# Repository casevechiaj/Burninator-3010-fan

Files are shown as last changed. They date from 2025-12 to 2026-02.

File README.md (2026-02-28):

# Burninator v2.2 💪🐉🔥
This toolhead is yet another 4010 toolhead, heavily inspired by the [Dragonburner](https://github.com/chirpy2605/voron/tree/main/V0/Dragon_Burner) and the [A4T](https://github.com/Armchair-Heavy-Industries/A4T/tree/main), all props to them.  
Thanks to Reddit user pd1zzle for suggesting the toolhead name, I really took a liking to it.  
And thanks to Reddit user linuxgangster for suggesting, testing, and providing feedback for the MadMax toolchanger adaptation.
 
<p>
 

</p>
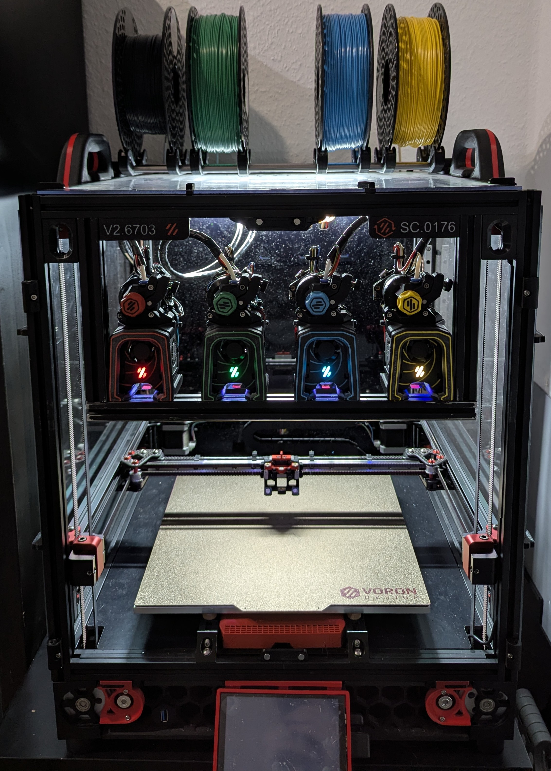
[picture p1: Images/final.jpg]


## But why?  
I created this toolhead because I wasn’t quite happy with the current toolhead options for my Stealthchanger.
Therefore, I decided to create my own toolhead to suit my use case and my printer.
I took features from the Dragonburner and the A4T and put them together, resulting in the Burninator.

## What its features?
It is small, smaller than the already compact Dragonburner, yet it can hold a UHF hotend, in this case the Dropeffect Next G Fiber with the UHF adapter, without missing out on nozzle and logo LEDs.
A monolithic cowl like the A4T cuts down the number of printed parts, screws, and heat inserts, increases rigidity, and simplifies assembly and disassembly.
Having a wall thickness of 1.2 mm makes the cowl more robust.  
It also adopts the A4Ts backflow inhibitor for decent part cooling performance.  



## Hotend compatibility:
- For the SF cowl, any Pheatus Dragon like hotends should fit i.e.: NextG, TZ.
- For the UHF cowl, any Pheatus Dragon UHF like hotend should fit i.e.: NextG UHF, Rapido HF, Dragon ACE (with the spacer)
- The CHC-XL got it own cowls 
- Rapido UHF got it own cowls

## Anything else?  
Besides the Rapido UHF, CHC-XL, UHF and SF toolheads, there are: 
- MGN12H invertable (Voron-2 / Monolith Gantry mod), MGN9H (pandora's gantry mod) and MGN7H (Voron-0) carriage, with x-endstop and both, klicky or Beacon/Cartographer(+spacer) mount, for standalone, non-toolchanger printers 
- StealthChanger toolchanger: backplate, ajustable docks with inbuild PTFE whiper and spring steel blocker, adapter for DraftShft docks
- MadMax toolchanger: backplate, docks with inbuild spring steel blocker and optinal PTFE whiper, modified SF and UHF cowls to work with MadMax.

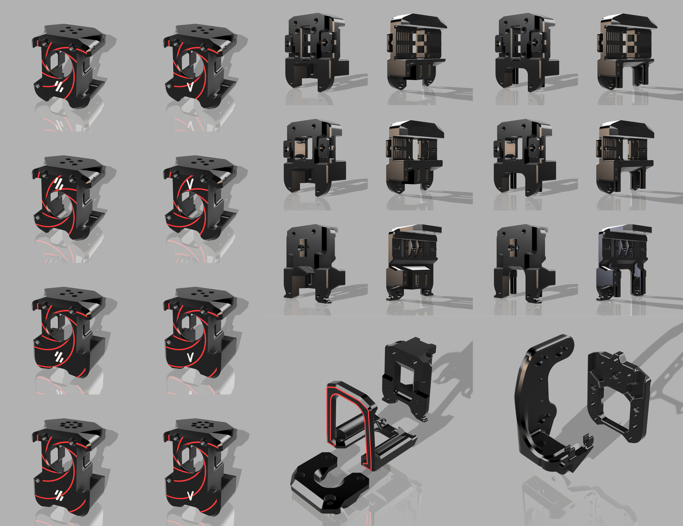
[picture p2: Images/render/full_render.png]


## What is planed?
For now, not much. 
You can also do request and I can take a look at it and upload it in the future. 
Of course, CAD files are available for you to mod it to your needs.

## How to Assemble?
Here's the [BOM](https://github.com/The-Duke-96/Burninator/blob/main/BOM.md).      
Here's a handy-dandy [Assembly manual](https://github.com/The-Duke-96/Burninator/blob/main/Assembly%20Manual.md).   

## Disclaimer:
- It turns out that when using printed parts for the Z-joints, the toolhead might be so small that the carriage of the Z linear rail hits the bottom of the frame before the toolhead touches the print bed for probing or leveling, since I have used a CNC kit for those parts from the beginning, I didn’t notice or consider it, a simple workaround is to add taller spacers or washers beneath the print bed, or use a diffrent, shorter Z-joints.
- Because the dock is quite small and space-saving, when using a door buffer for the StealthChanger, the DraftShift_dock_adapter needs to be used, otherwise the shuttle won’t reach the toolheads.
- If you use Beacon/Cartographer on CHC-XL or Rapido-UHF cowl, you need to extend the spacers to the correct lenght.
- StealthChanger and MadMax docks are designed for the SF and UHF cowls. I do not plan to adapt them for CHC XL or Rapido UHF, simply because a toolchanger already sacrifices print volume, and the smaller SF and UHF cowls are better suited for that use case. 
- For many files I have not received any feedback and, or could not test them myself, so if something is not working or not fitting, please let me know.
- Stock StealthChanger pickup and dropoff paths should work just fine, it might need some adjusment for the nozzle to scrub over the whiper.  If you like, you can use my custom paths:

```
params_dropoff_path: [{'y': 25, 'z':3}, {'y': 5, 'z':3} , {'y':0, 'z':3, 'f':0.5}, {'y':0, 'z':0, 'f':0.5}, {'y':0, 'z':-10}]
params_pickup_path: [{'y':0, 'z':-10}, {'y':0, 'z':0, 'f':0.5, 'verify':1}, {'y':0, 'z':3, 'f':0.5}, {'y': 25, 'z':3}]
```

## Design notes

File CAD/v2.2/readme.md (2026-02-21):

# CAD .step file

- Use these files if you wish to modify something. 
- “Burninator_RAW.step” offers a clean base version of the Burninator, with no cosmetics, no spiral pattern, no extruder mounts, and no front LED logo, so you can use it as a foundation to build on.
- Keep in mind that the fan duct must blow air to the correct area: the tip of the hotend nozzle should sit about 1.5 mm beneath the lowest part of the cowl.
- The CAD files do not include the subtraction for the MadMax screw holes on the cowls, in order to keep the file size down.
The component called “cowl_screwhole_extensions” in Burninator, MadMax is exactly what it says. Combine it with any cowl of your choice, do the screw hole subtraction, and you are done.

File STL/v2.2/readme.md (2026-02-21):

# STL Files

- All printed parts are already oriented correctly for printing.
- Required print supports are built in.
- cowls and its cosmetics are uploaded in one file as .3MF, no aligning in slicer needed anymore
- For the LED diffuser, it's recommended to print it in white or clear filament. You can also leave out the logo LED and print it in any color you want.
- You do not have to print the cowls in two colors, you can combine the two objects in the slicer, or simply print both in the same color.
- If you are using Cartographer or Beacon with the Rapido UHF or CHC XL cowl, do not forget to scale the spacer to the correct length.

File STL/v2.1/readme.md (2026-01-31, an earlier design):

# STL Files

- All printed parts are already oriented correctly for printing.
- Required print supports are built in.
- Cosmetics and their corresponding parts must be printed together, just align them and decide if and how you want to color them.  
**Note:** Aligning the cosmetic to the cowl, either eyeball it or use the following reference offsets:  
UHF cowl on X0/Y0, cosmetic X-1,75/Y0.35  
SF cowl on X0/Y0, cosmetic X0/Y-2.03

- For the LED diffuser, it's recommended to print it in white or clear filament. You can also leave out the logo LED and print it in any color you want.

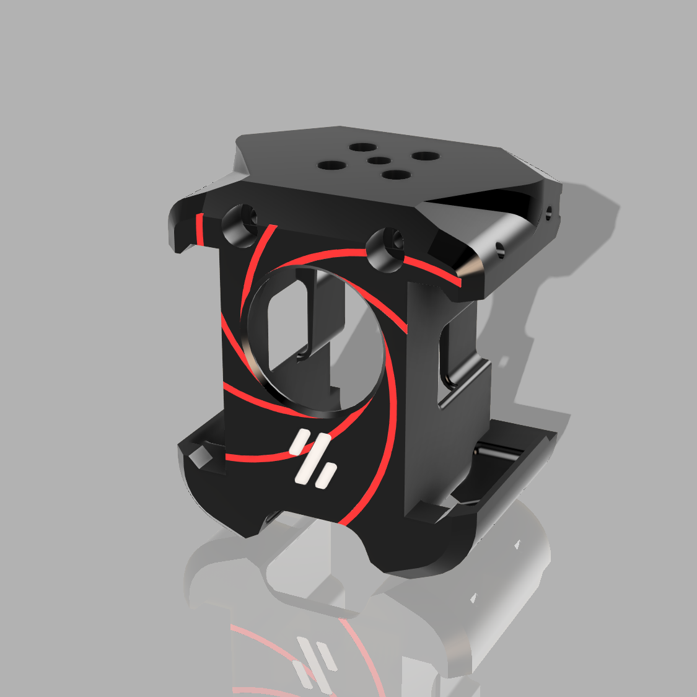
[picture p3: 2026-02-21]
Images/render/UHF_voron.png

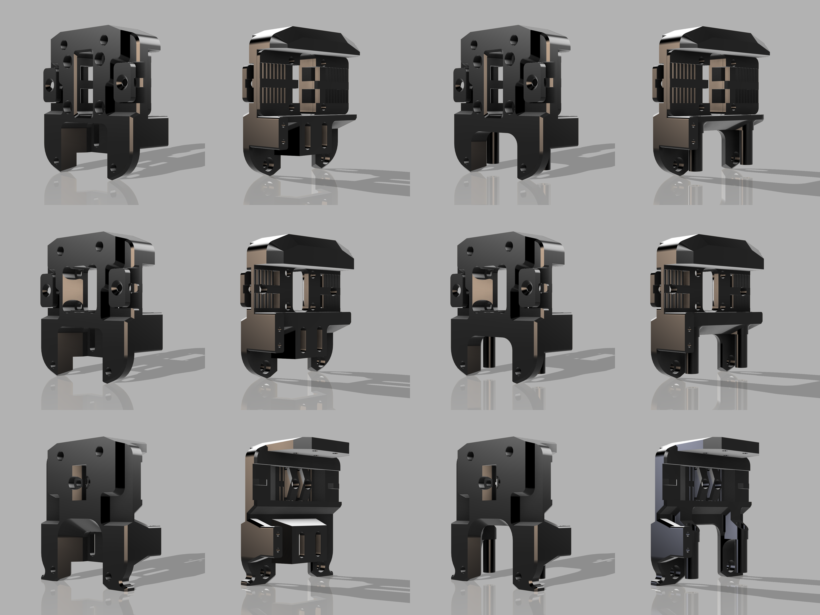
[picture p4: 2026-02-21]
Images/render/MGNxH_carriage.png

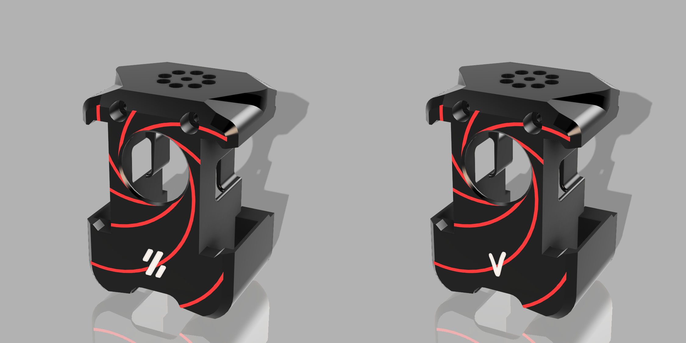
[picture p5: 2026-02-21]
Images/render/CHC-XL_cowl.png

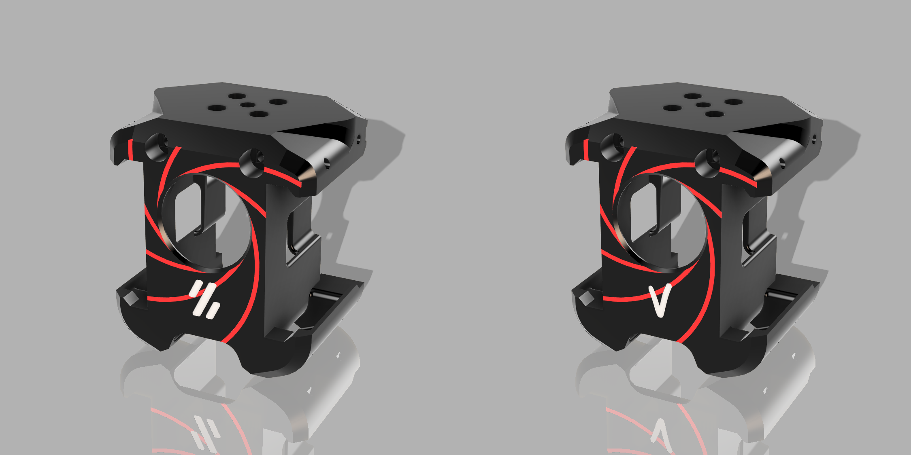
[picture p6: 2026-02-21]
Images/render/UHF_cowl.png

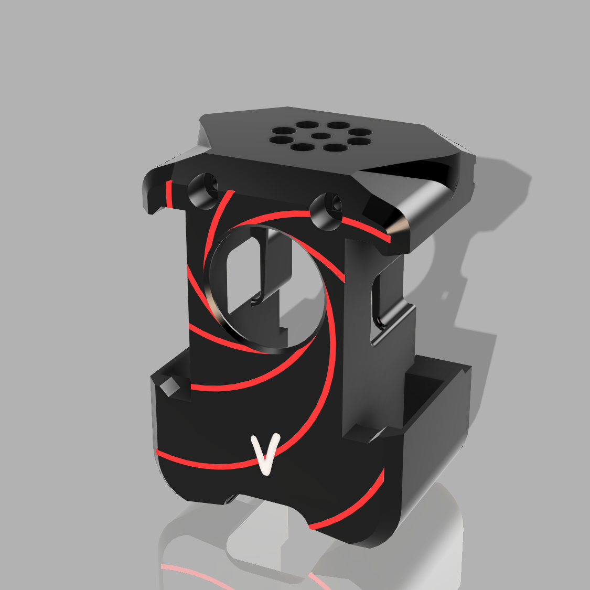
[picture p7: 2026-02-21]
Images/render/CHC-XL_consummate-V.png

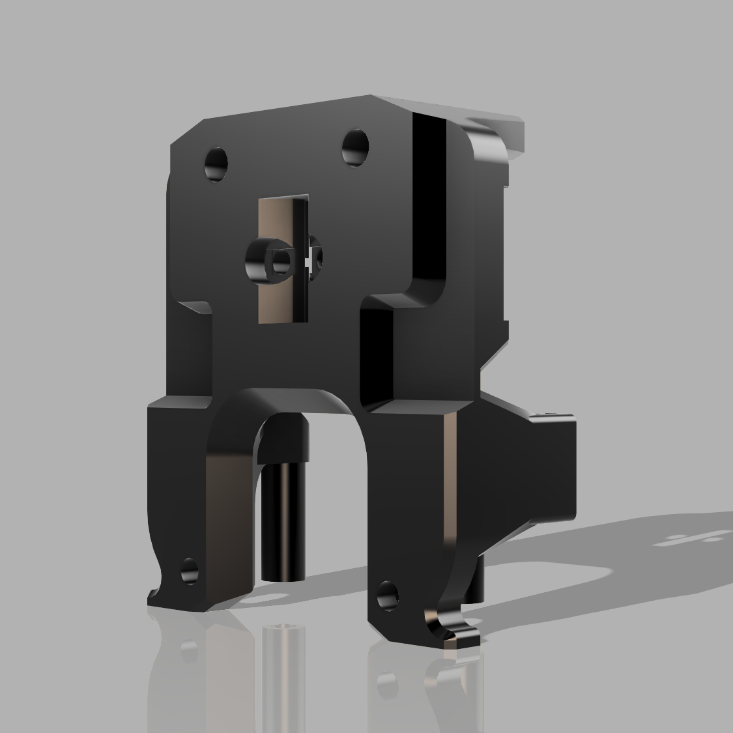
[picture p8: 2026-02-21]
Images/render/MGN7H_front_beacon_cartographer.png

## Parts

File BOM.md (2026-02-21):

# BOM

## Heat inserts
- 4x M3x4 on cowl
- 3x M3x4 on dock (stealthchanger)
- 1x M3x4 on dock (madmax)
- 2x M3x4 on stealthchanger backplate
- 2x M3x4 on MGN7H/MGN9H/MGN12H klicky carriage
- 4x M3x4 on MGN7H/MGN9H/MGN12H beacon/cartographer carriage
- 2x m3x4 on LGX Adapter
- 2x m3x4 on EBB36 mount
- 2x M5 on DraftShift Adapter

## Screws
- 2x M3x35 SHCS to secure cowl to backplate and MGN7H, MGN9H or MGN12H
- 2x M3x6 SHCS to secure cowl to backplate and MGN7H, MGN9H or MGN12H
- 2x M3x5 FHCS to secure belt clamps on MGN7H, MGN9H or MGN12H carriage
- 4x M3x10 to secure MGN9H or MGN12H carriage to linear rail
- 4x M3x6 to secure MGN7H carriage to linear rail
- 2x M3x6 SHCS to secure dock back
- 1x M3x5 BHCS to secure spring steel blocker
- 4x M5x8 BHCS to secure stealthchanger dock to DraftShift adapter and 2020 extrusion or crossbar
- 2x M5x8 BHCS to secure maxmax dock to 2020 extrusion or crossbar
- 2x M3x16 standoff on extruder back
- 2x M3x6 BHCS to secure EBB36 mount to standoffs
- 2x M3x6 BHCS to secure EBB36 PCB to mount
- 2x M3x6 BHCS to secure optotap to backplate
- 2x M3x6 SHCS to secure LGX adapter to cowl
- 2 M3x20 BHCS to secure beacon/cartographer to carriage (longer screws needed for CHC-Xl and Rapido UHF cowl)

## Others
- 1x 2510 fan 24V
- 2x 4010 fan 24V
- 3x RGB PCB LEDs (NeoPixel or simular)
- 1x PTFE tube 21mm (stealthchanger dock)
- 1x PTFE tube 25mm (madmax dock)
- 1x spring steel blocker 7x29mm cut from old tape measure (stealthchanger dock)
- 1x spring steel blocker 5x36mm cut from old tape measure (madmax dock)
- 2x magnets 3x6mm N52 (stealthchanger dock)
- 3x magnets 3x6mm N52 (madmax dock)

## Also you might want to check out those other BOMs:  
MadMax: https://github.com/zruncho3d/madmax/blob/main/BOM.md  
StealthChanger: https://github.com/DraftShift/StealthChanger/wiki/Bill-of-Materials

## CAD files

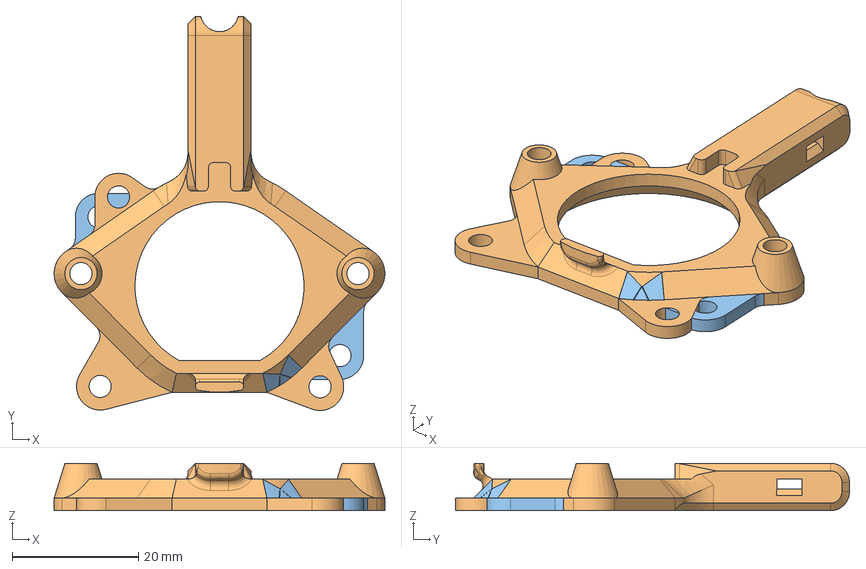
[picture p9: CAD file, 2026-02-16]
CAD/v2.2/EBB36_Mount.step
52.3 x 62.3 x 7.50 mm

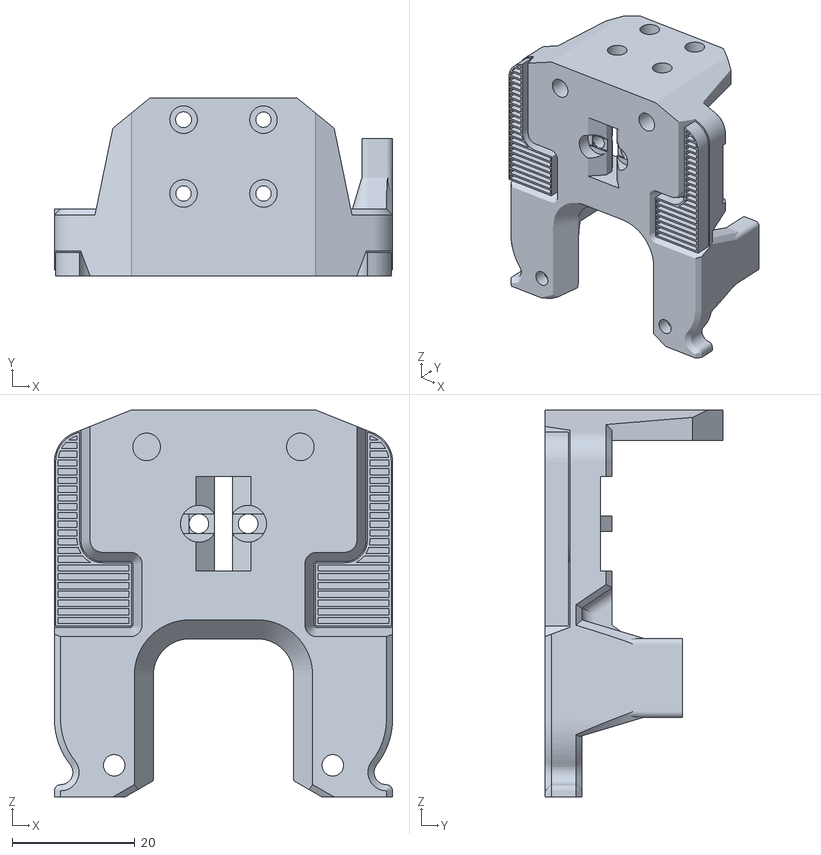
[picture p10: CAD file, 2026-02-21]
STL/v2.2/Carriage/MGN7H_carriage_beacon_cartographer.stl
55.0 x 28.9 x 62.9

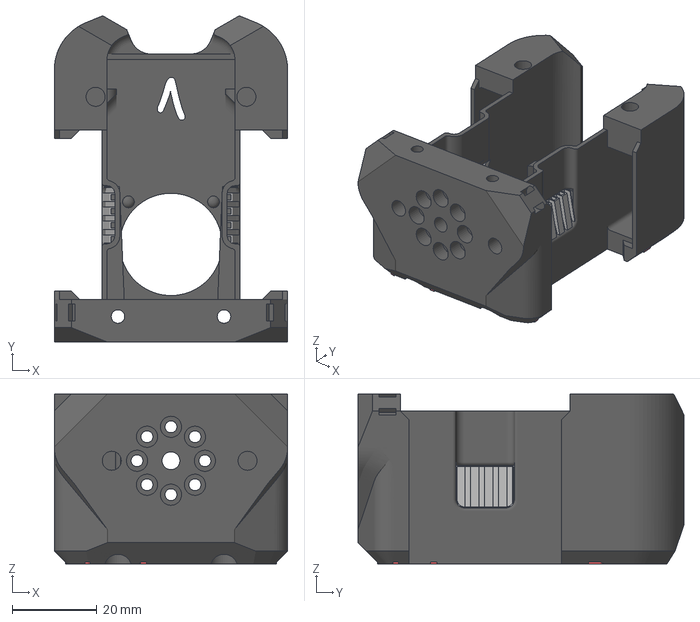
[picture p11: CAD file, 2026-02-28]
STL/v2.2/cowls_3MF/CHC-XL/consummate-V_logo/CHC_consummate-V_sherpa-micro.3mf
55.0 x 76.8 x 40.0 mm

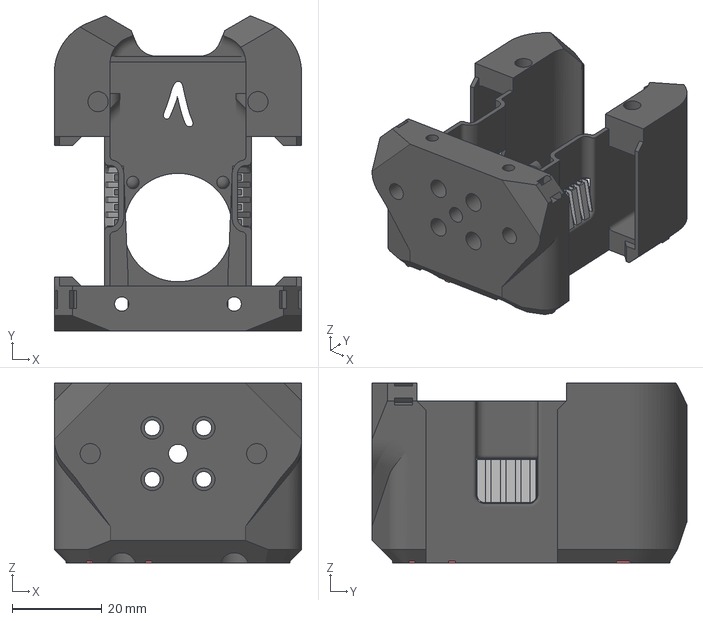
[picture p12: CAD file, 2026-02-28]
STL/v2.2/cowls_3MF/Rapido_UHF/consummate-V_logo/Rapido_UHF_consummate-V_orbiter.3mf
55.0 x 70.0 x 40.0 mm

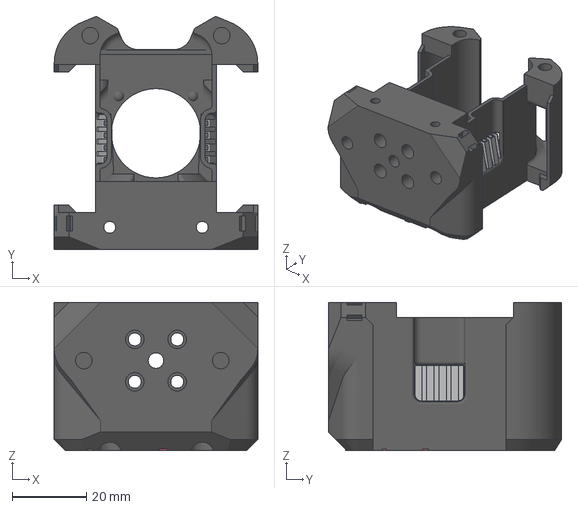
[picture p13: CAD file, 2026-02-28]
STL/v2.2/cowls_3MF/SF/consummate-V_logo/SF_consummate-V_orbiter.3mf
55.0 x 62.9 x 40.0 mm

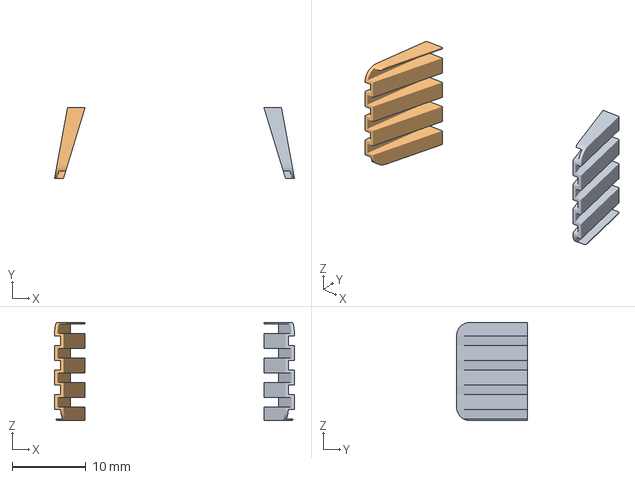
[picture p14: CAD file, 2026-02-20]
STL/v2.2/cowls_3MF/support.3mf
32.5 x 9.60 x 13.3 mm
Körper1
Körper4

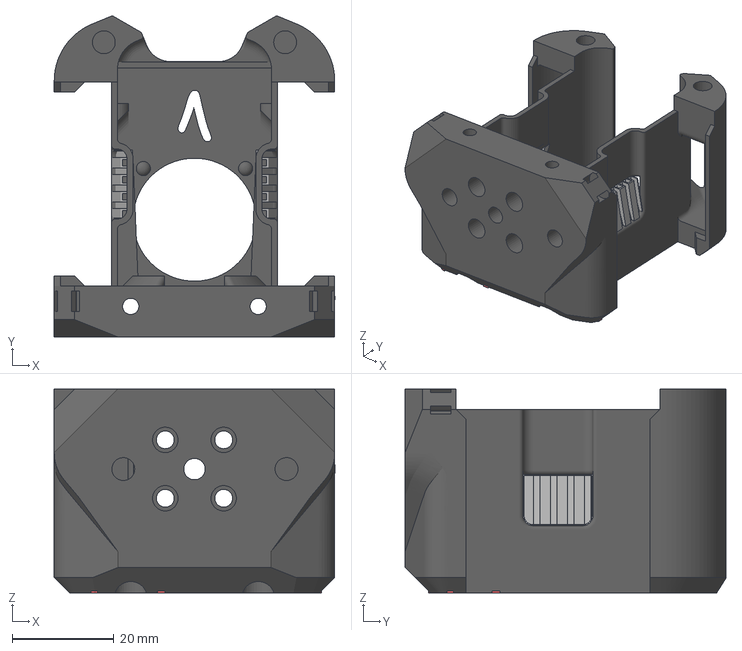
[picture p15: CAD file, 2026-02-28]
STL/v2.2/cowls_3MF/UHF/consummate-V_logo/UHF_consummate-V_sherpa_micro.3mf
55.0 x 62.9 x 40.0 mm

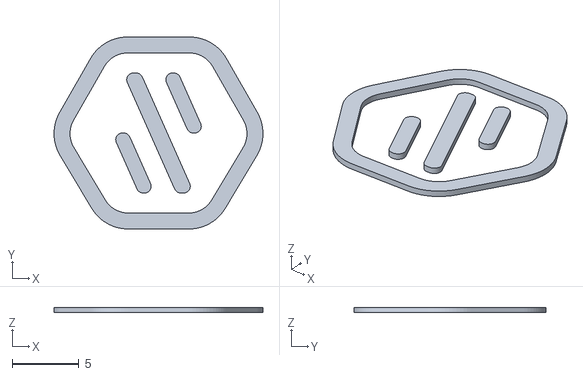
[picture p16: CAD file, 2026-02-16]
STL/v2.2/Knob_logo.stl
15.7 x 14.4 x 0.4

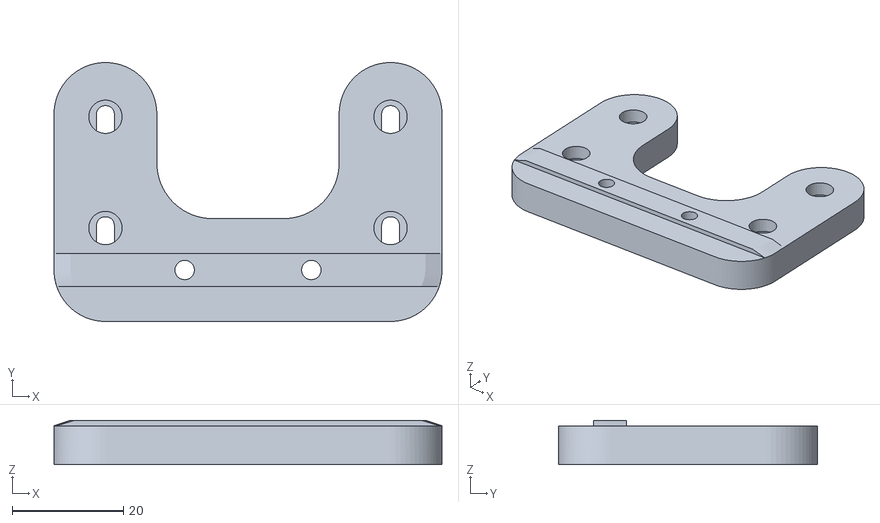
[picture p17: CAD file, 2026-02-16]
STL/v2.2/MadMax/MadMax_Burninator_Dock.stl
69.8 x 46.6 x 8.00

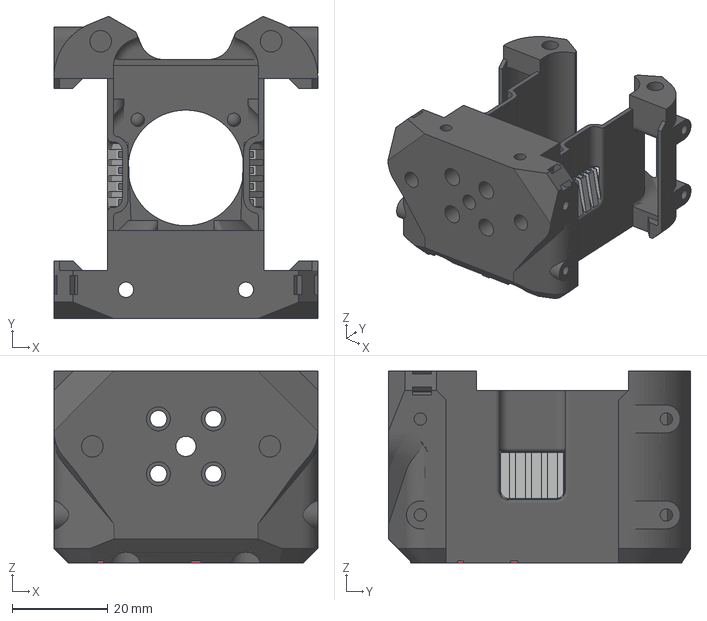
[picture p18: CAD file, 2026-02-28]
STL/v2.2/MadMax/MadMax_cowls_3MF/SF/consummate-V_logo/SF_consumate-V_orbiter.3mf
55.0 x 62.9 x 40.0 mm

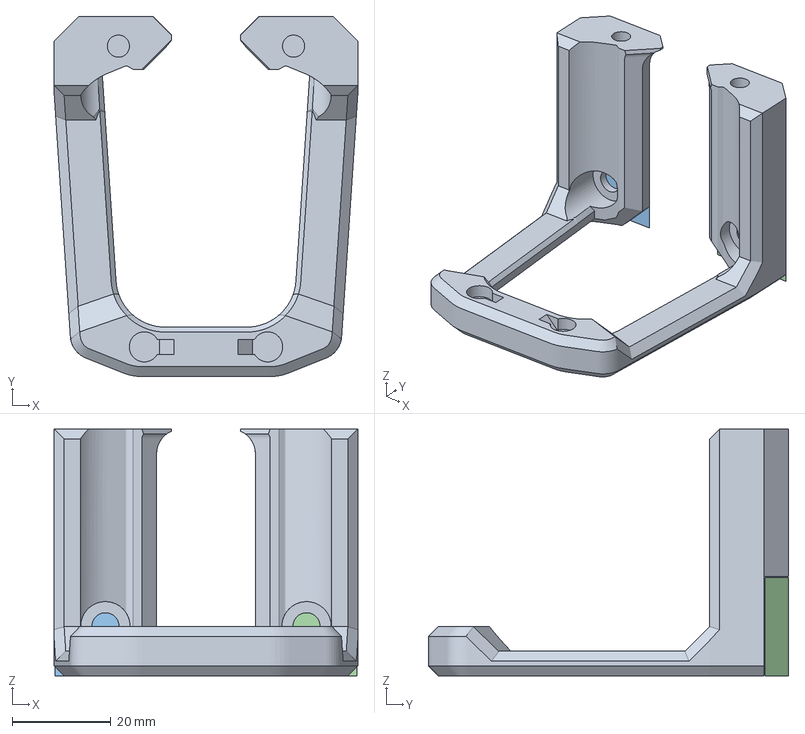
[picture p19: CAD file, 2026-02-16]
STL/v2.2/StealthChanger/dock_adjustable.3mf
61.5 x 72.9 x 50.0 mm

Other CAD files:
STL/v2.2/cowls_3MF/CHC-XL/voron_logo/CHC_Voron_ECAS.3mf
STL/v2.2/cowls_3MF/Rapido_UHF/voron_logo/Rapido_UHF_voron_orbiter.3mf
STL/v2.2/cowls_3MF/SF/voron_logo/SF_Voron_sherpa_mini.3mf
STL/v2.2/cowls_3MF/UHF/voron_logo/UHF_Voron_orbiter.3mf
STL/v2.2/MadMax/MadMax_cowls_3MF/SF/voron_logo/SF_voron_sherpa-micro.3mf
STL/v2.2/MadMax/MadMax_cowls_3MF/UHF/consummate-V_logo/UHF_consumate-V_orbiter.3mf
STL/v2.2/MadMax/MadMax_cowls_3MF/UHF/voron_logo/UHF_Voron_ECAS.3mf
CAD/v2.1/EBB36_Mount.step
CAD/v2.2/Knob.step
STL/v2.1/A4T Backflow Inhibitor install spacer tool.stl
STL/v2.1/CHC-XL/Cowl_CHC-XL_Cosmetic.stl
STL/v2.1/CHC-XL/Cowl_CHC-XL_ECAS_Bowden.stl
STL/v2.1/CHC-XL/Cowl_CHC-XL_Orbiter.stl
STL/v2.1/CHC-XL/Cowl_CHC-XL_Sherpa_Micro.stl
STL/v2.1/CHC-XL/Cowl_CHC-XL_Sherpa_Mini.stl
STL/v2.1/Knob.stl
STL/v2.1/Knob_Cosmetic.stl
STL/v2.1/LED_Diffuser.stl
STL/v2.1/LGX_Adapter_Orbiter.stl
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

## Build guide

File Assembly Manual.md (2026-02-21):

# Assembly Manual

- Start by installing the heat inserts: two in the bottom rear, two on top of the cowl, two at the top of either the StealthChanger backplate or the MGN12H / MGN7H / MGN9H klicky carriage plus two more on the backside on beacon/cartographer carriage, two in the back of the EBB mount, one in the bottom of the dock, two in the back of the dock and two M5 inserts in the dock adapter.

<p>
 


 
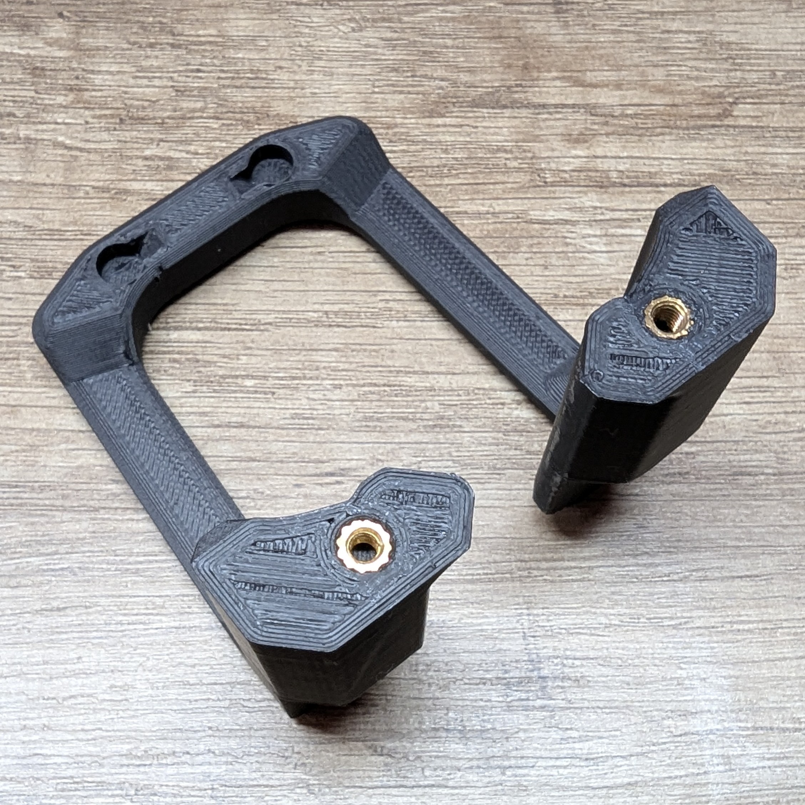
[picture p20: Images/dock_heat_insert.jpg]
 
 
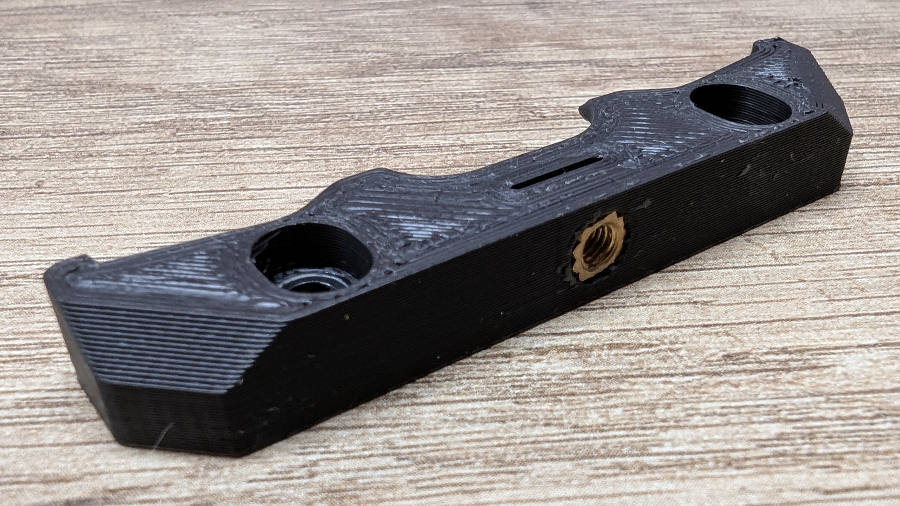
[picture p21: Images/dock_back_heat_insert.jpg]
 
</p>

- Insert the 2510 fan from the back and slide it upward, wedging it into place. The two small nubs should fit into the bottom holes of the fan, securing it further. This works the same way as on the Dragonburner.
- Insert the LED diffuser into the Voron logo cutout.



- Continue with soldering the LEDs. You'll need six pieces of 20mm wire and three pieces of 170mm wire.
- Solder the first three short wires to the OUT pads of the first LED.
- Solder the second LED, facing the opposite direction of the first.
- Solder the last three short wires to the second LED, facing the same direction as the first set.
- Solder the third LED so that it faces the same direction as the first LED and opposite the second.
- Solder the 170mm wire to the IN pads and crimp on the connector.  
  **Note:** Make sure the wires are soldered in the correct orientation as shown in the picture.
  
<p>
   
   
  
 
</p>

- Insert the second LED into the LED carrier first, then the remaining two, it’s easier that way.
- Insert the LED carrier from the back, placing the bottom edge into the cowl ledge. Tilt it, then press it firmly into place. Ensure the diffuser is seated in the front groove of the LED carrier.

<p>
   
   
</p>

- For the 4010 fans: remove the front cover and glue in A4T’s Backflow Inhibitor (optional but recommended).  
  After the glue has dried, put the cover pack on.
- One of the fans needs its wires bent toward the back. You may also resolder the wires.
- Slide the fans into the sides of the cowl, same as on the Dragonburner.

<p>
   
   
</p>

- Install the hotend. In my case, a Dropeffect NextG Fiber UHF is used. Ensure it's rotated correctly so the cables point toward the back corner.
- Route the thermistor wire with the cable sleeve to the opposite side, as it will not fit through the cowl and backplate cutouts. Route the heater wires on the other side, bending them so they will fit cleanly.



- Place the backplate, wiggle the cables into position, and ensure the metal hose sits inside the backplate groove underneath the center hole. Screw it down.
- Install either M3x40 SHCS screws with a 3 mm spacer, or M3x35 SHCS screws without the spacer and place a 6×3 mm magnet on top.
- Route cables into the grooves and secure them with zip-ties.
- If using the StealthChanger backplate, install the OptoTap PCB.
- If using Beacon/Cartographer carriage, now install the probe.

<p>
   
   
</p>

- Install a 22 mm PTFE tube and mount your extruder. In this example, the Galileo 2 WristWatch is used, followed by the toolhead PCB.
- In this setup, the EBB36_G2WW_Mount is required due to interference from the OptoTap.
- The toolhead is now complete.



---

# Cowl SF Assembly

- Assembling the SF cowl is only a little bit different from the UHF cowl.
- For soldering the LEDs, you need wires in the following lengths: 3 × 47 mm, 3 × 30 mm, and 3 × 170 mm.
- Start with the last LED and solder the 47 mm wires to the IN.
- Now solder the second LED, and then the first LED, using the 30 mm wires.
- Finally, solder the 170 mm wires and crimp on the connector.  
  **Note:** Make sure the wires are soldered in the correct orientation as shown in the picture.
- After that, place them into the LED carrier.

<p>


</p>

- Moving on to the cowl: first insert the LED diffuser and the top LED carrier. The cable should exit sideways into the cable channel.  
**Note:** Inside the cable channel are two little support ribs, as printing support. Just cut them away, 



- Then tuck the cable into the corner and run it down along the wall. Push the larger LED carrier aside and insert the 2510 fan.
- After that, push the larger LED carrier into place.  
  **Note:** Due to the tight space, routing the cable and seating everything can be a bit tricky. The better the soldering job and the thinner the wires, the easier it gets.



---

# Dock Assembly

- Take a 21 mm PTFE tube for the wiper and press it into the back holder.
- Press the magnets into the top.
- Screw on the back.
- Insert the 29 mm spring steel blocker into the rear slit and secure it with an M3x5 screw.
- Mount the dock onto the crossbar, optionally using the adapter.
- Dock the toolhead adjust the height of the back and the depth of the spring steel blocker

<p>
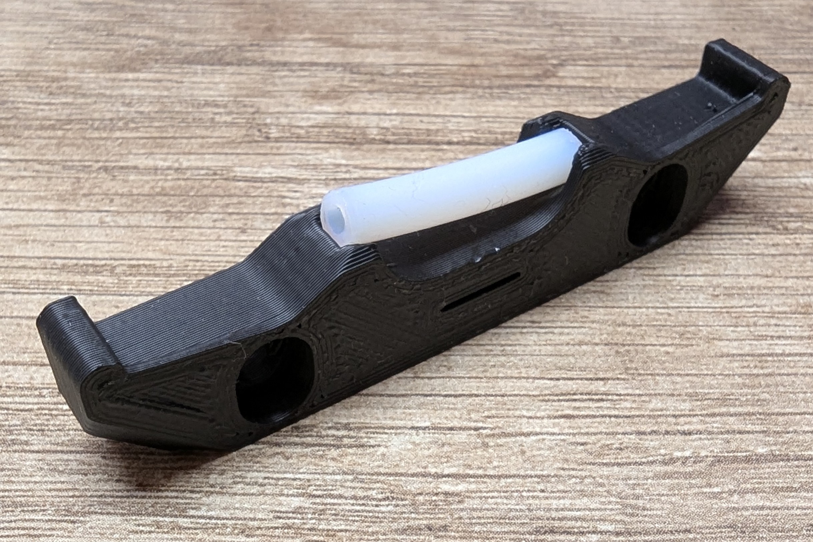
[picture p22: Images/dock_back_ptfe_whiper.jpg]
 
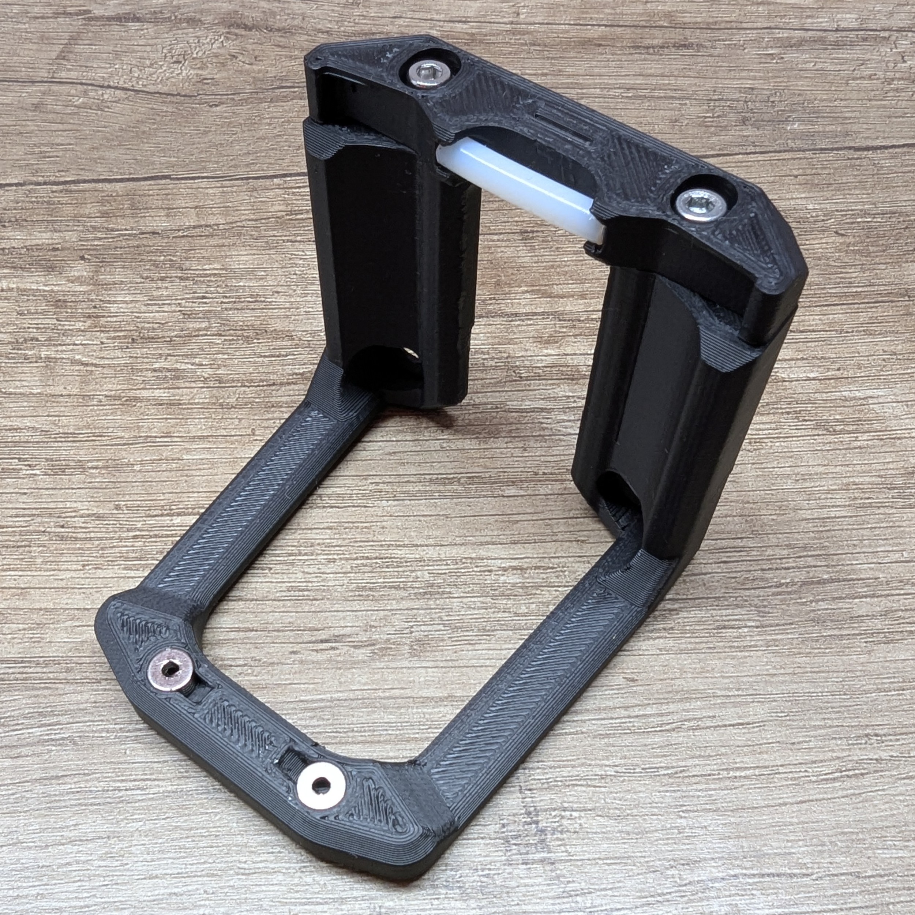
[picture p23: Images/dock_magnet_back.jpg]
 
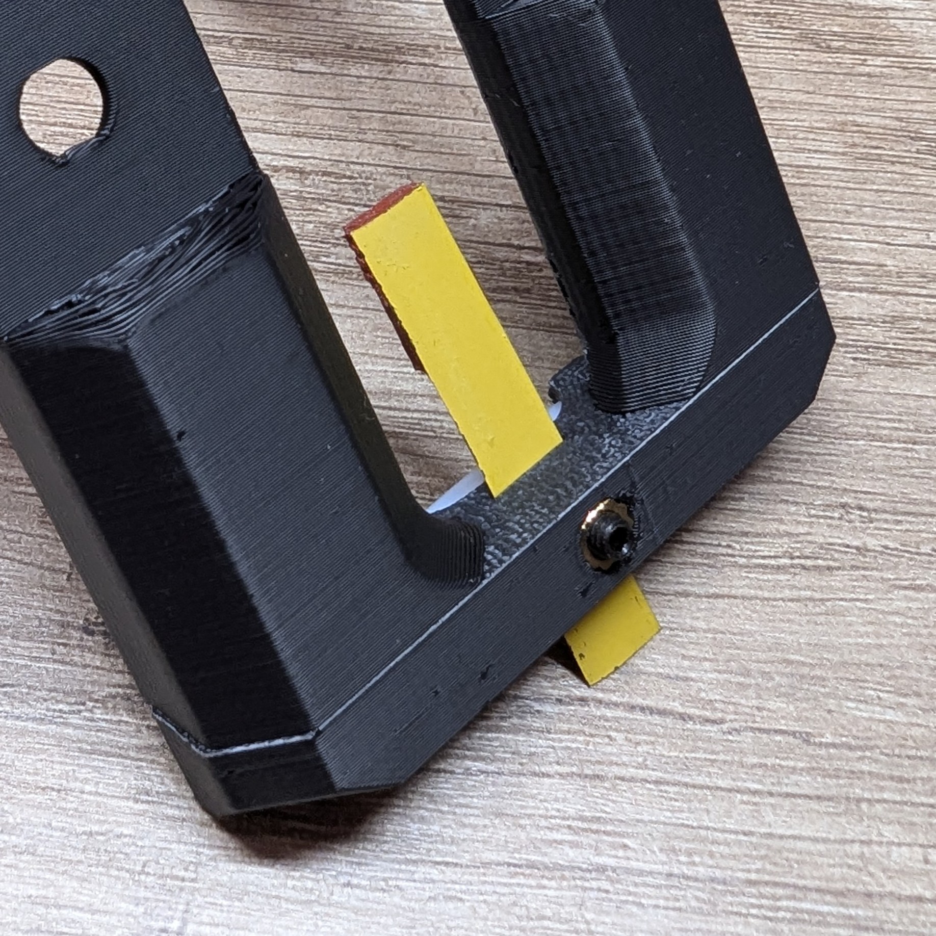
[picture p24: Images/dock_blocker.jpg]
   
  </p>

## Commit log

2025-12-18 Add image to README
    Added an image of the final toolhead to the README.
2025-12-21 Add assembly instructions
    Added detailed assembly instructions for the Assembly Manual, including steps for installing heat inserts, fans, LEDs, and the dock assembly.
2025-12-21 Cleanup assembly instructions in readme.md
    Removed assembly instructions for LED diffuser, fans, and toolhead. Updated notes for soldering LEDs and cable routing.
2025-12-21 Add Bill of Materials (BOM) for components
2025-12-21 Include BOM and assembly manual links
    Added links to BOM and assembly manual in the README.
2025-12-21 edited README
    Updated links for BOM and Assembly manual for clarity.
2025-12-21 Update BOM.md with revised heat insert details
2025-12-21 Clean up BOM.md by removing blank lines
    Removed extra blank lines in the screws section.
2025-12-21 Update BOM.md to specify SHCS for LGX adapter
2025-12-21 Clarify LED description in BOM
2026-01-24 Create readme.md in STL/Beta directory
    Add readme for temporary work in progress files
2026-01-30 Revise hotend compatibility details in README
    Updated hotend compatibility information for SF and UHF cowls.
2026-01-30 Fix formatting of hotend compatibility section
2026-01-30 Fix typo in Hotend compatibility section
2026-01-31 Reorganised some files
    [DraftShift_dock_adapter.stl, MadMax_Burninator_Backplate.stl, MadMax_Burninator_Dock.stl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]
2026-01-31 Deleted v1
    [Burninator_v1.step, Cowl_Cosmetic.stl, Cowl_NextG_Bowden_ECAS.stl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]
2026-02-16 added new version folders in CAD
    [A4T Backflow Inhibitor [x2].stl, CHC_Voron_ECAS.3mf, CHC_Voron_orbiter.3mf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]
2026-02-20 Updated 3MF files
    [CHC_Voron_ECAS.3mf, CHC_Voron_orbiter.3mf, CHC_Voron_sherpa_micro.3mf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]
2026-02-20 Revise hotend compatibility and toolhead details
    Updated compatibility details for toolheads and carriages.
2026-02-20 Update readme with details on Burninator_RAW.step
    Added description for 'Burninator_RAW.step' file and clarified fan duct positioning.
2026-02-21 update CAD files
    [MGN12H_carriage.stl, MGN12H_invertable_carriage_beacon_cartographer.stl, MGN12H_invertable_carriage_klicky.stl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]
2026-02-21 Fix formatting and enhance toolhead descriptions in README
    Corrected formatting and improved clarity in the description of toolheads and components.
2026-02-21 Update Assembly Manual.md
2026-02-21 Update readme with printing instructions for cowls
2026-02-21 Revise BOM for MGN7H/MGN12H carriage details
    Updated the BOM to reflect changes in carriage types and added a new carriage entry.
2026-02-21 Add M3x20 BHCS for beacon/cartographer mounting
2026-02-28 updating CAD files
2026-03-01 Add files via upload
    3010 Mod fitted for Tz v6 2.0 with MZE
    This was made in mind for a Creality CR6se so there may be some variances such as the holes on the sides for inserts. Also, just a warning, i'm not great with CAD lol
